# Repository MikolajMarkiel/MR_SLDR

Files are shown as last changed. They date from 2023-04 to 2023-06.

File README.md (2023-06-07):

# WARNING!

The project is in build stage. Missing documentation and functionalities will be added in time.

# Overview

The MR_SLDR is a project of remote controlled slider for camera. It will be controlled by Bluetooth Low Energy protocol. The main library source for this project is Zephyr OS.

# How to run

# Software description

## Web_bluetooth

## timer

Due to problems with flexibility occurence of threads in zephyr (minimal period step is 100us) I've decided to leave control of stepper motor up to hardware timer peripheral. Unfortunately right now esp32 timer drivers are dedicated only for counters that lose synchronization after overflow of counted ticks. Because of that I had to add extra modification to counter_esp32_tmr.c file (this file is a driver to handle every action of timer after setting devicetree &timerX status = "okay"). The modification allow us to decide that counter will autoreset after getting alarm or won't. It doesn't harm any project that use old driver, because for this to work user has to add extra `COUNTER_AUTORESET` config to Kconfig file. I've included new counter_esp32_tmr.c file in bin/ directory. The path for replacement is `../zephyrproject/zephyr/drivers/counter/counter_esp32_tmr.c`

## Distance_meter

# Hardware description

## Power section

The main supply for the board is +5V microUSB port. It supplies two DC-DC converters: step-up to +12V and step-down to +3,3V. The +12 DC voltage is needed for charging alternative power supply based on 3 li-ion cells driven by BMS3451 BMS. If there is no USB cable connected, then step-down converter is supplied by +12V instead. There is an external switch that enables step-down converter. If it is disabled, then every peripheral would be powered down except stepper motor driver which would go into sleep mode instead. Connecting USB cable with switch turned off allow charging batteries without turning on the device.
Voltage level of cell block is continually checked by ADC, and the feedback information is given to user via BLE.

## CPU & programming

An ESP32 module has been chosen as a CPU for the device. It has been because of his low cost and support for bluetooth communication and zephyr OS. There are two ways to communicate PC with CPU: via CP2102 USB to UART bridge module connected to micro USB and JTAG connector. Both allow to program flash memory. Additionally the bridge provides serial communication with PC and JTAG give possibility to debug software.

## Stepper motor driver

DRV8825 module has been used as an output driver for stepper motor. It provides easy interface because of it's STEP/DIR functionality. For more information please refer to datasheet of module.

## Distance meter

For checking actual position of camera even after power off the laser distance meter VL53LXX module is connected to CPU by I2C interface. Because it is needed to connect module directly at path of moving camera, then the module has been removed from the main hardware PCB and case. For more information please refer to datasheet of module.

## Camera control blocks

There are also two isolated switches for example for activating remote control of camera or other these types activities. They are designed with use of single channel transoptors PC817.

## EEPROM

The board provides also external EEPROM (M93C76C module) for saving user data of slider settings. It communicates with CPU via SPI interface.

## Mechanicals

The board has been designed for Z57J universal case (https://www.kradex.com.pl/product/enclosures_hermetically_sealed/z57j_ps?lang=en) but it is also possible to print something similar. By now there is no need to provide additional 3D models of case.

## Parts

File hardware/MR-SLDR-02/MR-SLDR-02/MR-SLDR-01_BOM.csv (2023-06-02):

Source: | /home/mikolaj/projects/MR-SLDR/hardware/MR-SLDR-01/MR-SLDR-01.kicad_sch
Date: | pią, 2 cze 2023, 03:15:36
Tool: | Eeschema 7.0.2-6a45011f42~172~ubuntu22.04.1
Generator: | /usr/share/kicad/plugins/bom_csv_grouped_by_value.py
Component Count: | 139
Collated Components:
Item | Qty | Reference(s) | Value | LibPart | Footprint | Datasheet | DNP | MANUFACTURER | MAXIMUM_PACKAGE_HEIGHT | PARTREV | STANDARD | Sim.Device | Sim.Pins | Sim.Type
1 | 7 | Batt.meas1, TP3, TP4, TP5, TP6, TP7, TP8 | TestPoint | Connector:TestPoint | TestPoint:TestPoint_THTPad_1.0x1.0mm_Drill0.5mm | ~
2 | 2 | C1, C19 | 680uF | Device:C_Polarized | Capacitor_THT:CP_Radial_D10.0mm_P5.00mm | ~
3 | 15 | C2, C3, C4, C5, C6, C8, C9, C10, C12, C13, C15, C21, C22, C29, C30 | 100nF | Device:C | Capacitor_SMD:C_0805_2012Metric_Pad1.18x1.45mm_HandSolder | ~
4 | 2 | C11, C14 | 470uF | Device:C_Polarized | Capacitor_THT:CP_Radial_D8.0mm_P3.80mm | ~
5 | 1 | C16 | none | Device:C | Capacitor_SMD:C_0805_2012Metric_Pad1.18x1.45mm_HandSolder | ~
6 | 3 | C17, C18, C23 | 470nF | Device:C | Capacitor_SMD:C_0805_2012Metric_Pad1.18x1.45mm_HandSolder | ~
7 | 1 | C20 | 4.7uF | Device:C | Capacitor_SMD:C_1206_3216Metric_Pad1.33x1.80mm_HandSolder | ~
8 | 1 | C24 | 100uF | Device:C_Polarized | Capacitor_THT:CP_Radial_D8.0mm_P3.80mm | ~
9 | 4 | C25, C26, C27, C28 | 10nF | Device:C | Capacitor_SMD:C_0805_2012Metric_Pad1.18x1.45mm_HandSolder | ~
10 | 3 | D1, D2, D3 | SS24 | SS24:SS24 | bin:DIOM5336X265N |  |  | ON Semiconductor | 2.65 mm | 1.1.2 | IPC 7351B
11 | 1 | D4 | SP0503BAHT | Power_Protection:SP0503BAHT | Package_TO_SOT_SMD:SOT-143 | http://www.littelfuse.com/~/media/files/littelfuse/technical%20resources/documents/data%20sheets/sp05xxba.pdf
12 | 1 | D5 | 10V | Device:D_Zener | Diode_SMD:D_MiniMELF | ~
13 | 1 | D6 | BAT54S | Diode:BAT54S | Package_TO_SOT_SMD:SOT-23 | https://www.diodes.com/assets/Datasheets/ds11005.pdf
14 | 1 | F1 | Fuse | Device:Fuse | Fuse:Fuse_1206_3216Metric_Pad1.42x1.75mm_HandSolder | ~
15 | 4 | H1, H2, H3, H4 | MountingHole | Mechanical:MountingHole | MountingHole:MountingHole_3.2mm_M3 | ~
16 | 4 | J1, J8, J9, J10 | Conn_01x02_Pin | Connector:Conn_01x02_Pin | Connector_Molex:Molex_SL_171971-0002_1x02_P2.54mm_Vertical | ~
17 | 1 | J2 | Conn_01x04_Pin | Connector:Conn_01x04_Pin | Connector_Molex:Molex_KK-254_AE-6410-04A_1x04_P2.54mm_Vertical | ~
18 | 1 | J3 | USB_B_Micro | Connector:USB_B_Micro | Connector_USB:USB_Micro-B_Amphenol_10118194_Horizontal | ~
19 | 1 | J4 | Conn_02x05_Odd_Even | Connector_Generic:Conn_02x05_Odd_Even | Connector_PinHeader_2.00mm:PinHeader_2x05_P2.00mm_Vertical | ~
20 | 1 | J5 | Conn_01x04_Socket | Connector:Conn_01x04_Socket | Connector_Molex:Molex_KK-254_AE-6410-04A_1x04_P2.54mm_Vertical | ~
21 | 1 | J6 | Conn_01x06_Pin | Connector:Conn_01x06_Pin | Connector_Molex:Molex_KK-254_AE-6410-06A_1x06_P2.54mm_Vertical | ~
22 | 1 | J7 | Conn_02x04_Odd_Even | Connector_Generic:Conn_02x04_Odd_Even | Connector_PinSocket_2.54mm:PinSocket_2x04_P2.54mm_Vertical | ~
23 | 4 | JP1, JP7, JP8, JP9 | SolderJumper_2_Bridged | Jumper:SolderJumper_2_Bridged | Jumper:SolderJumper-2_P1.3mm_Bridged_RoundedPad1.0x1.5mm | ~
24 | 5 | JP2, JP3, JP4, JP5, JP6 | SolderJumper_2_Open | Jumper:SolderJumper_2_Open | Jumper:SolderJumper-2_P1.3mm_Open_RoundedPad1.0x1.5mm | ~
25 | 1 | L1 | 33uH | Device:L | Inductor_SMD:L_12x12mm_H8mm | ~
26 | 1 | L2 | 22uH | Device:L | Inductor_SMD:L_TDK_VLF10040 | ~
27 | 6 | Q1, Q2, Q6, Q7, Q8, Q9 | BC817 | Transistor_BJT:BC817 | Package_TO_SOT_SMD:SOT-23 | https://www.onsemi.com/pub/Collateral/BC818-D.pdf
28 | 1 | Q3 | IRLML6402 | Transistor_FET:IRLML6402 | Package_TO_SOT_SMD:SOT-23 | https://www.infineon.com/dgdl/irlml6402pbf.pdf?fileId=5546d462533600a401535668d5c2263c
29 | 2 | Q4, Q5 | QM6006D | Transistor_FET:QM6006D | Package_TO_SOT_SMD:TO-252-2 | http://www.jaolen.com/images/pdf/QM6006D.pdf |  |  |  |  |  | NMOS | 1=D 2=G 3=S | VDMOS
30 | 14 | R1, R2, R3, R7, R14, R15, R16, R19, R26, R30, R31, R43, R44, R47 | 1k | Device:R | Resistor_SMD:R_0805_2012Metric_Pad1.20x1.40mm_HandSolder | ~
31 | 2 | R4, R8 | 5M | Device:R | Resistor_SMD:R_0805_2012Metric_Pad1.20x1.40mm_HandSolder | ~
32 | 3 | R5, R10, R20 | 3k | Device:R | Resistor_SMD:R_0805_2012Metric_Pad1.20x1.40mm_HandSolder | ~
33 | 1 | R6 | 220k | Device:R | Resistor_SMD:R_0805_2012Metric_Pad1.20x1.40mm_HandSolder | ~
34 | 3 | R9, R11, R35 | 1M | Device:R | Resistor_SMD:R_0805_2012Metric_Pad1.20x1.40mm_HandSolder | ~
35 | 7 | R12, R32, R33, R34, R38, R41, R42 | 10k | Device:R | Resistor_SMD:R_0805_2012Metric_Pad1.20x1.40mm_HandSolder | ~
36 | 1 | R13 | 2k | Device:R | Resistor_SMD:R_0805_2012Metric_Pad1.20x1.40mm_HandSolder | ~
37 | 4 | R17, R18, R22, R23 | 5m | Device:R | Resistor_SMD:R_2512_6332Metric_Pad1.40x3.35mm_HandSolder | ~
38 | 1 | R21 | 1.8k | Device:R | Resistor_SMD:R_0805_2012Metric_Pad1.20x1.40mm_HandSolder | ~
39 | 4 | R24, R39, R40, R48 | 100k | Device:R | Resistor_SMD:R_0805_2012Metric_Pad1.20x1.40mm_HandSolder | ~
40 | 1 | R25 | 11k | Device:R | Resistor_SMD:R_0805_2012Metric_Pad1.20x1.40mm_HandSolder | ~
41 | 1 | R27 | 24k | Device:R | Resistor_SMD:R_0805_2012Metric_Pad1.20x1.40mm_HandSolder | ~
42 | 1 | R28 | 47k | Device:R | Resistor_SMD:R_0805_2012Metric_Pad1.20x1.40mm_HandSolder | ~
43 | 1 | R29 | 4,7k | Device:R | Resistor_SMD:R_0805_2012Metric_Pad1.20x1.40mm_HandSolder | ~
44 | 2 | R36, R37 | 100m | Device:R | Resistor_SMD:R_1206_3216Metric_Pad1.30x1.75mm_HandSolder | ~
45 | 3 | R45, R46, R49 | none | Device:R | Resistor_SMD:R_0805_2012Metric_Pad1.20x1.40mm_HandSolder | ~
46 | 1 | RN1 | 1k | Device:R_Pack04 | Resistor_SMD:R_Array_Convex_4x1206 | ~
47 | 1 | RV1 | 100k | Device:R_Potentiometer | Potentiometer_THT:Potentiometer_Bourns_3296W_Vertical | ~
48 | 1 | TP1 | +3.3V | Connector:TestPoint | TestPoint:TestPoint_THTPad_1.0x1.0mm_Drill0.5mm | ~
49 | 1 | TP2 | +12V | Connector:TestPoint | TestPoint:TestPoint_THTPad_1.0x1.0mm_Drill0.5mm | ~
50 | 1 | U1 | BM3451 | BM3451:BM3451(20pin) | Package_SO:TSSOP-20_4.4x6.5mm_P0.65mm
51 | 1 | U2 | ~ | axelite:AX3007ESA | Package_SO:SOIC-8-1EP_3.9x4.9mm_P1.27mm_EP2.29x3mm
52 | 1 | U3 | ~ | axelite:AX5201 | Package_SO:SOIC-8-1EP_3.9x4.9mm_P1.27mm_EP2.29x3mm
53 | 1 | U4 | ESP32-WROOM-E | Espressif:ESP32-WROOM-E | Espressif:ESP32-WROOM-32E | https://www.espressif.com/sites/default/files/documentation/esp32-wroom-32e_esp32-wroom-32ue_datasheet_en.pdf
54 | 1 | U5 | CP2102N-Axx-xQFN28 | Interface_USB:CP2102N-Axx-xQFN28 | Package_DFN_QFN:QFN-28-1EP_5x5mm_P0.5mm_EP3.35x3.35mm | https://www.silabs.com/documents/public/data-sheets/cp2102n-datasheet.pdf
55 | 1 | U6 | DRV8825 | DRV8825:DRV8825 | Package_SO:HTSSOP-28-1EP_4.4x9.7mm_P0.65mm_EP3.4x9.5mm_ThermalVias
56 | 1 | U7 | 93CxxC | Memory_EEPROM:93CxxC | Package_SO:SO-8_3.9x4.9mm_P1.27mm | http://ww1.microchip.com/downloads/en/DeviceDoc/20001749K.pdf
57 | 2 | U8, U9 | PC817 | Isolator:PC817 | Package_DIP:DIP-4_W7.62mm | http://www.soselectronic.cz/a_info/resource/d/pc817.pdf

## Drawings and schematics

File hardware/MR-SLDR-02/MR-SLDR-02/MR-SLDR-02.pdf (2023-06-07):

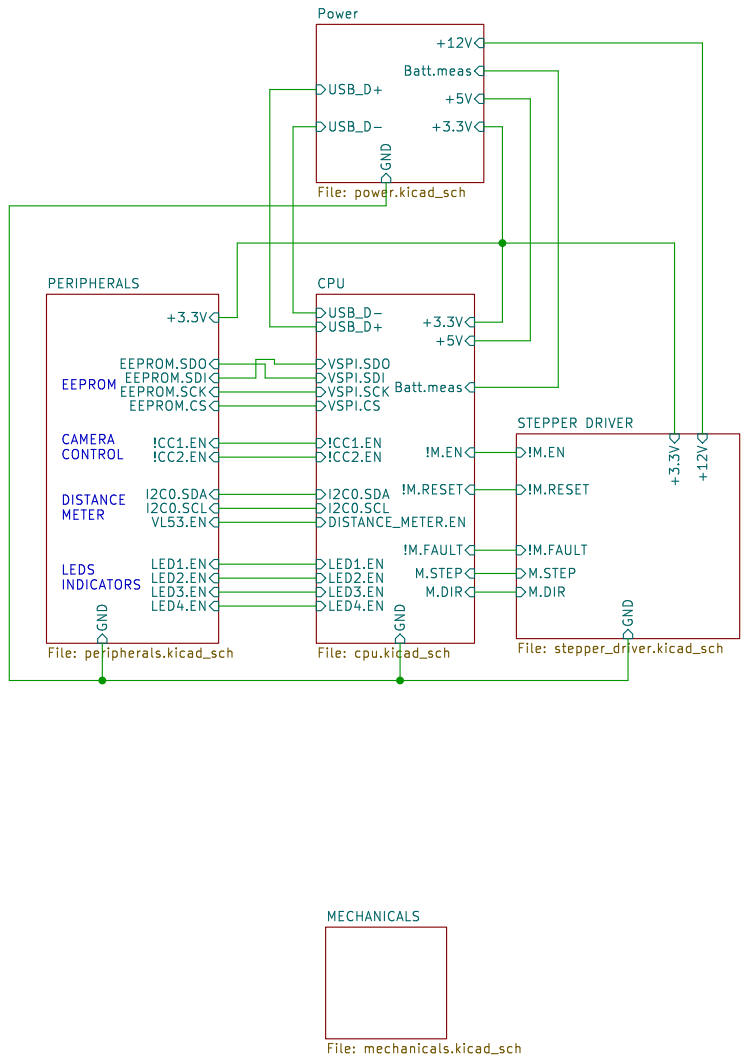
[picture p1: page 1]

Batt.meas Power File: power.kicad_sch GND

EEPROM.SDO
EEPROM.SDI EEPROM.CS
EEPROM.SCK

!M.FAULT VSPI.SDO
VSPI.SDI VSPI.SCK DISTANCE_METER.EN
VSPI.CS

CAMERA CONTROL DISTANCE METER

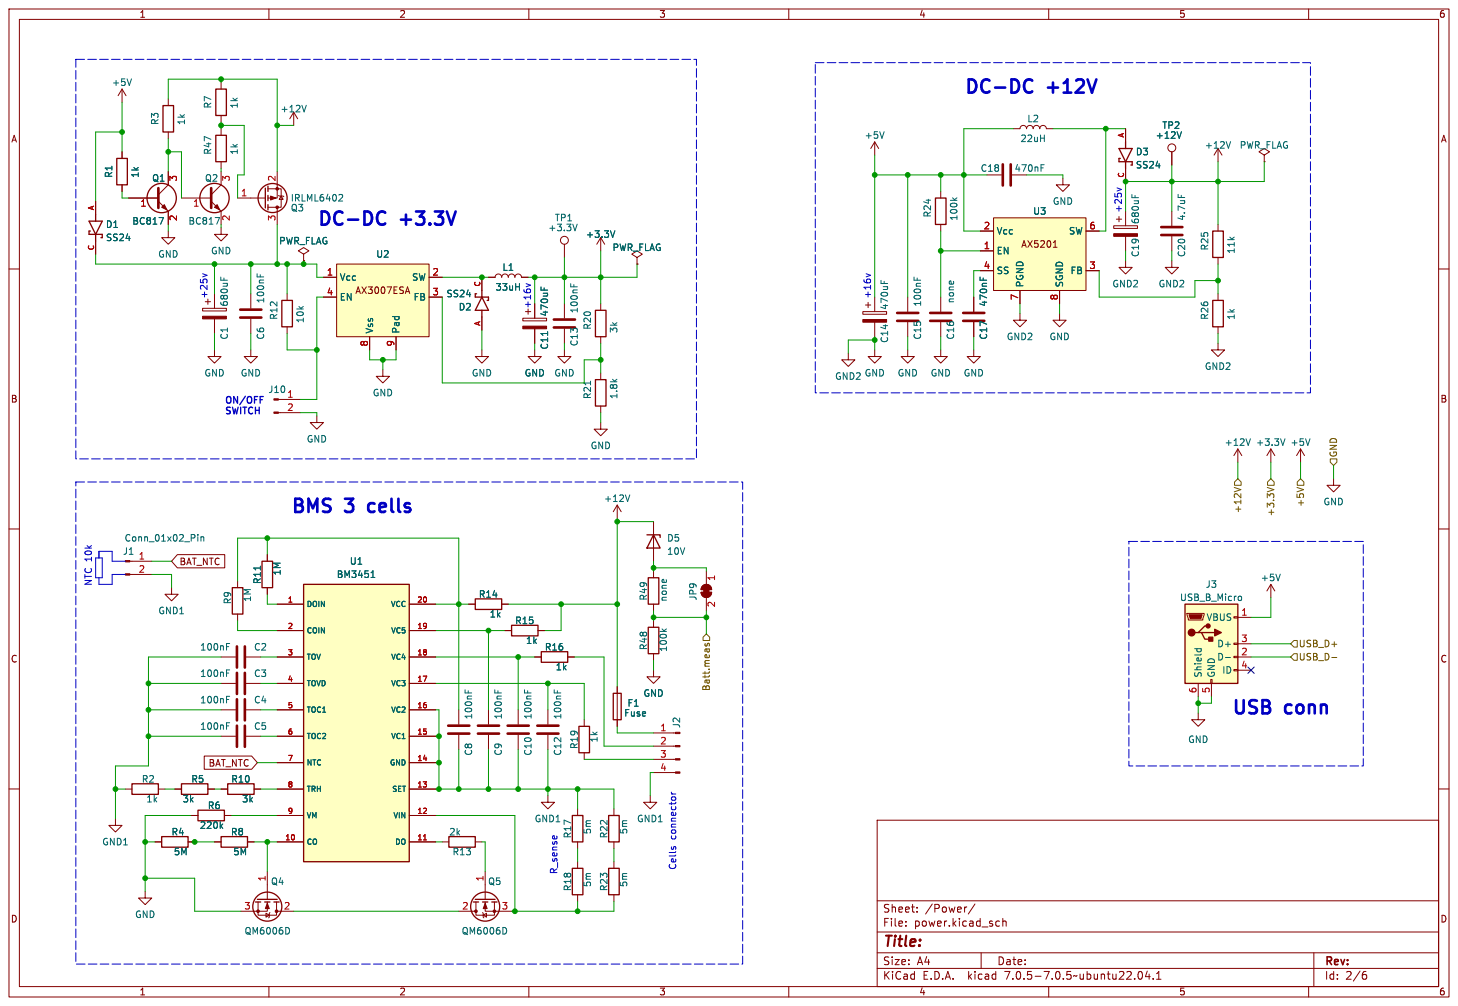
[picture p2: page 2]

A C U3 EN 1 Vcc 2 FB 3 SS 4 SW 6 PGND

Id: 2/6 Title: File: power.kicad_sch Sheet: /Power/

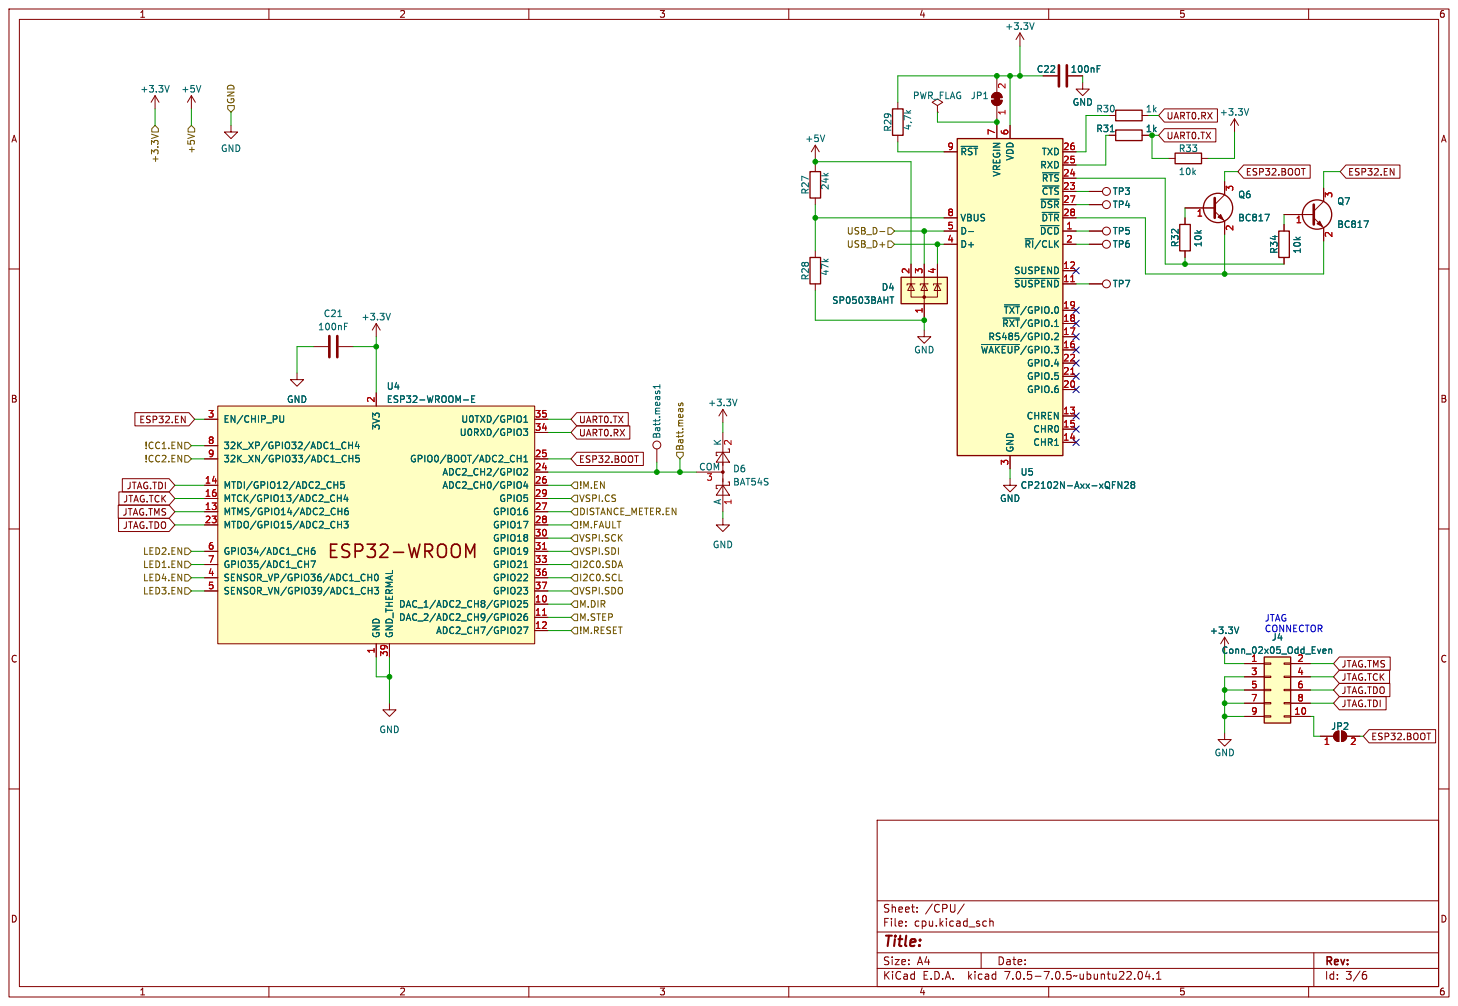
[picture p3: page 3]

4 U5 CP2102N-Axx-xQFN28 ~{DCD}1 ~{SUSPEND}11 SUSPEND 12 CHREN 13 CHR1 14 CHR0 15 ~{WAKEUP}/GPIO.316 RS485/GPIO.2 17 ~{RXT}/GPIO.118 ~{TXT}/GPIO.019 ~{RI}/CLK2 GPIO.6 20 GPIO.5 21 GPIO.4 22 ~{CTS} 23 ~{RTS} 24 RXD 25 TXD 26 ~{DSR} 27 ~{DTR} 28 GND

JTAG.TDI JTAG.TDO

DISTANCE_METER.EN
!M.FAULT VSPI.SDI VSPI.SCK

JTAG.TDI JTAG.TMS
JTAG.TCK
JTAG.TDO

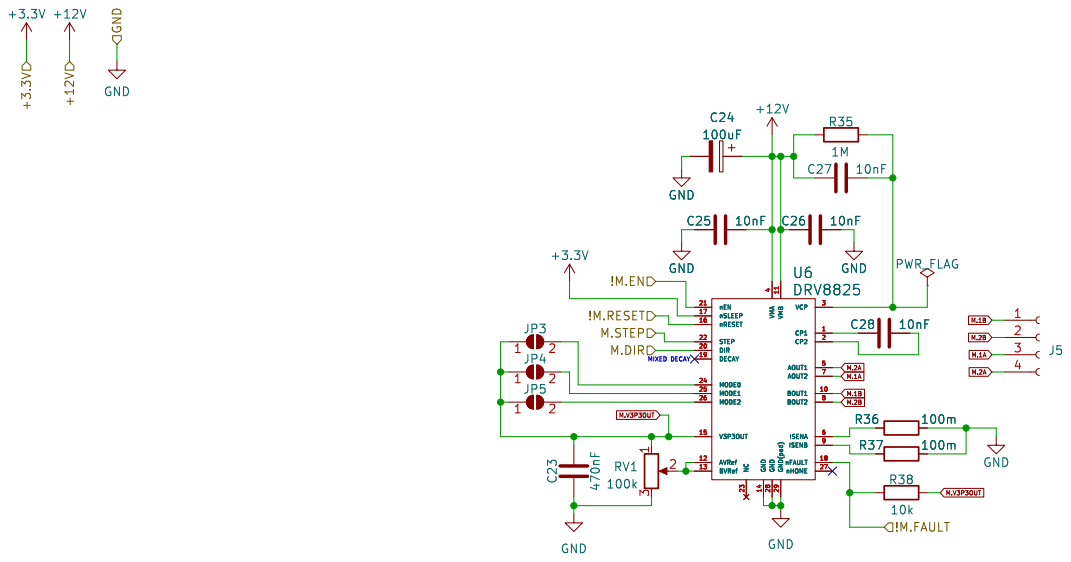
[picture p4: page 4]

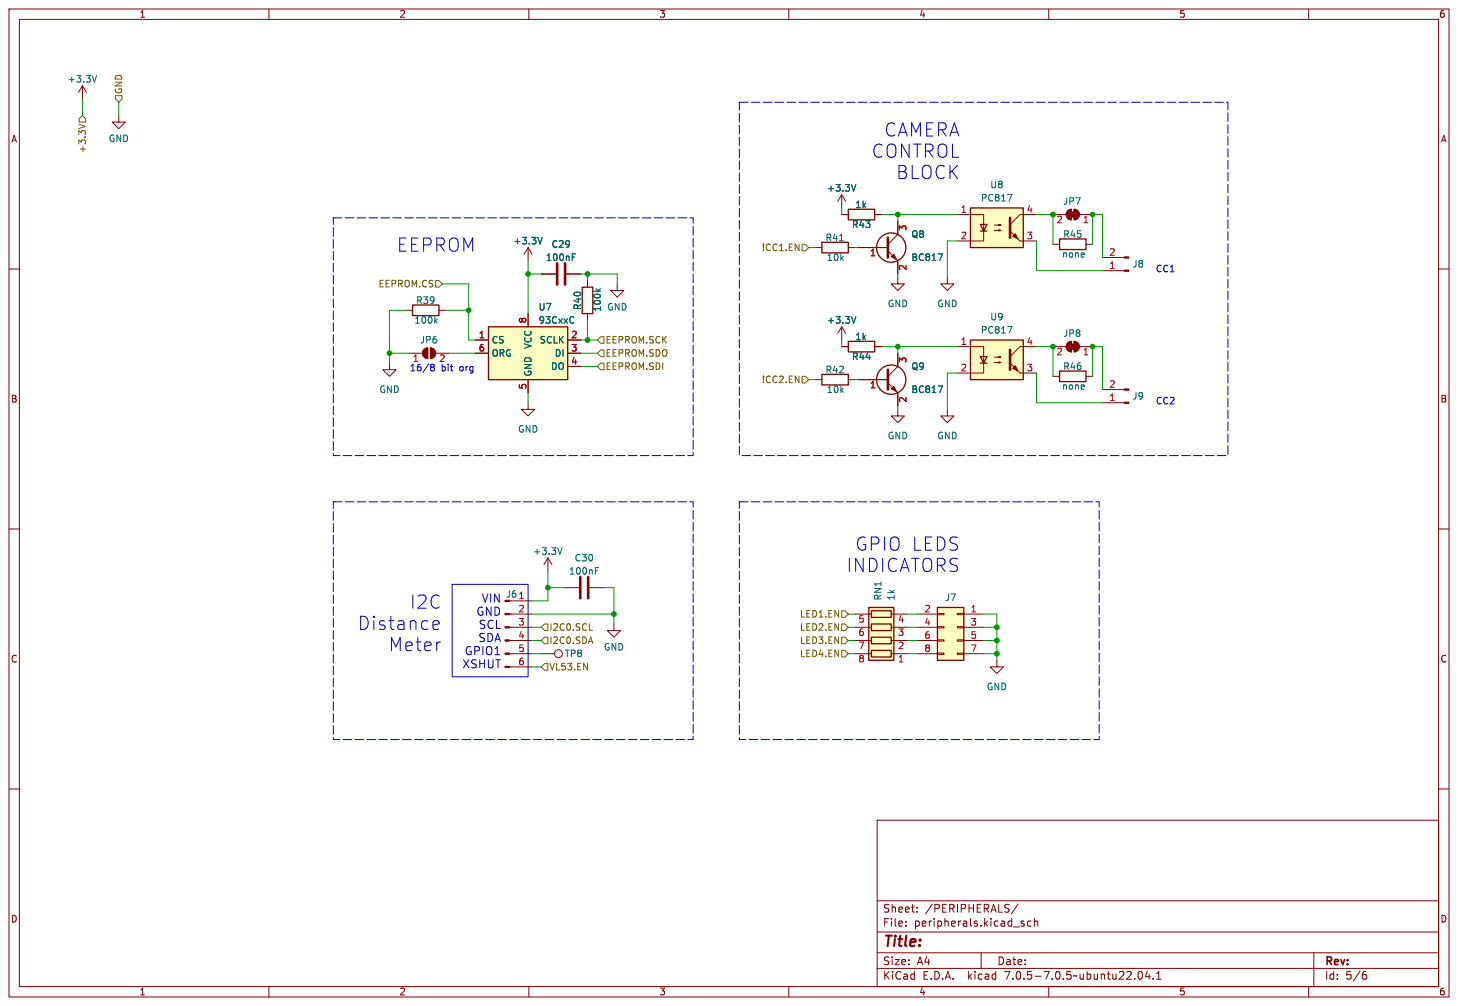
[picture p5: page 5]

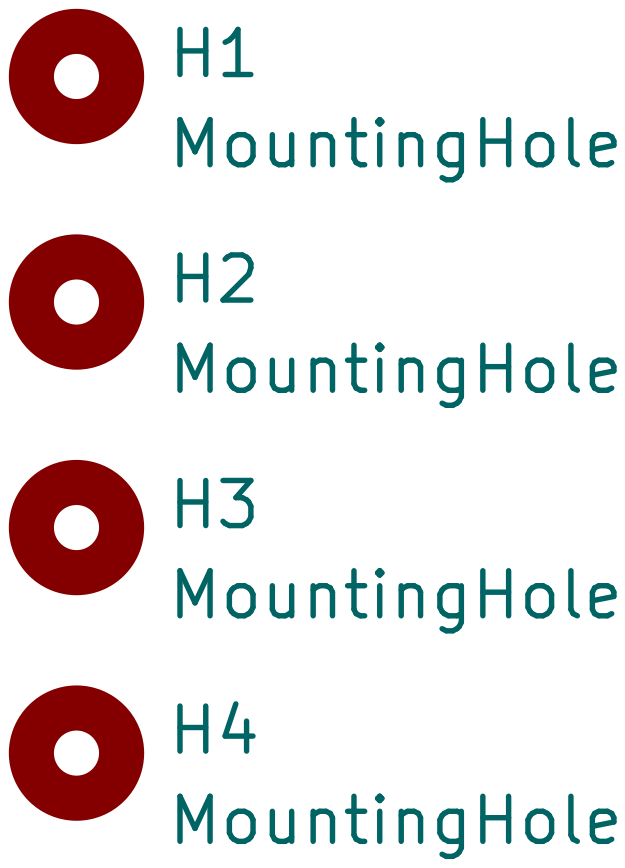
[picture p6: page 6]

H3 MountingHole H4 MountingHole H1 MountingHole H2 MountingHole

Id: 6/6 Title: File: mechanicals.kicad_sch Sheet: /MECHANICALS/

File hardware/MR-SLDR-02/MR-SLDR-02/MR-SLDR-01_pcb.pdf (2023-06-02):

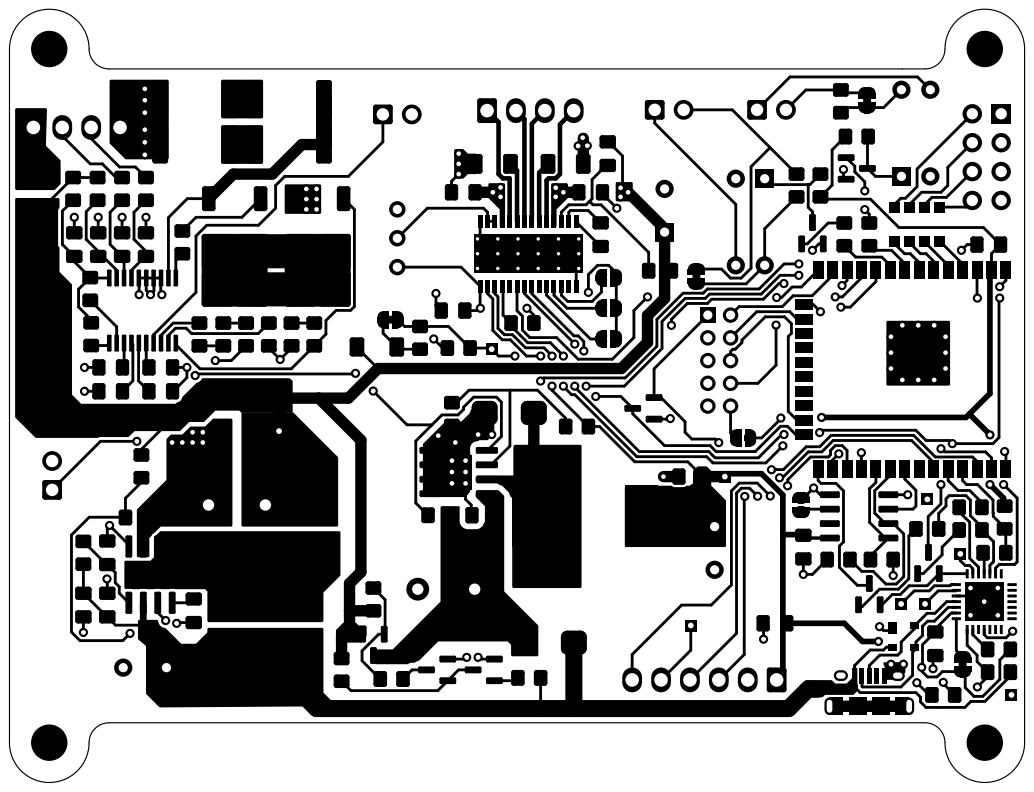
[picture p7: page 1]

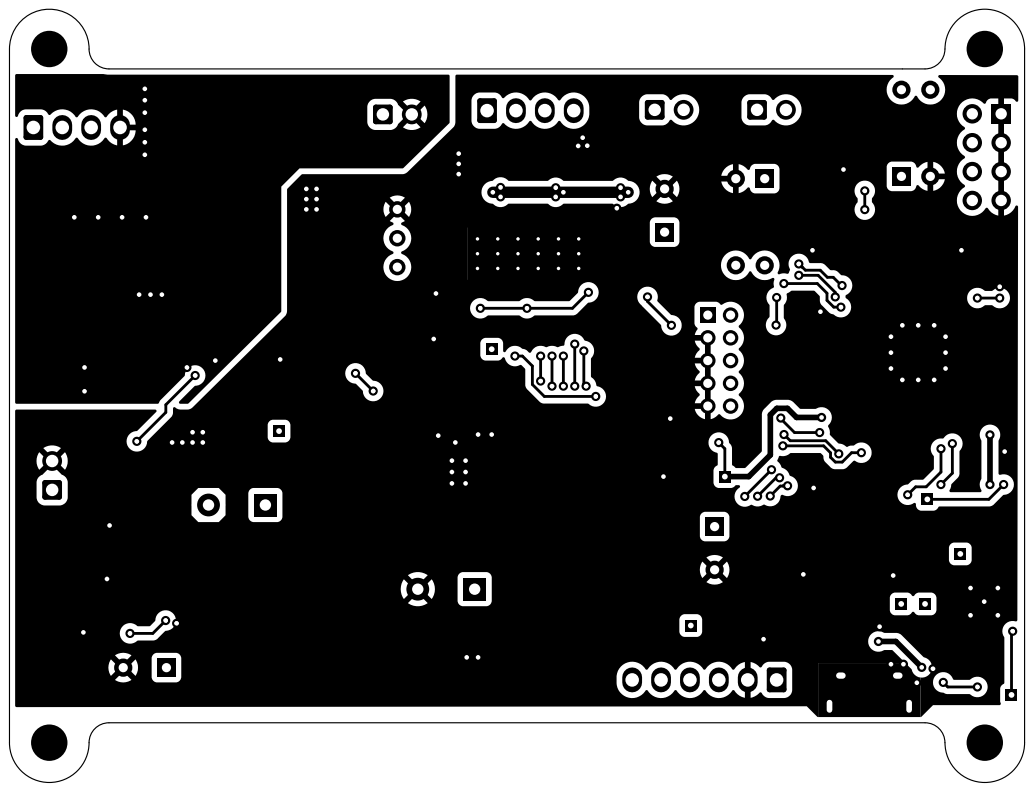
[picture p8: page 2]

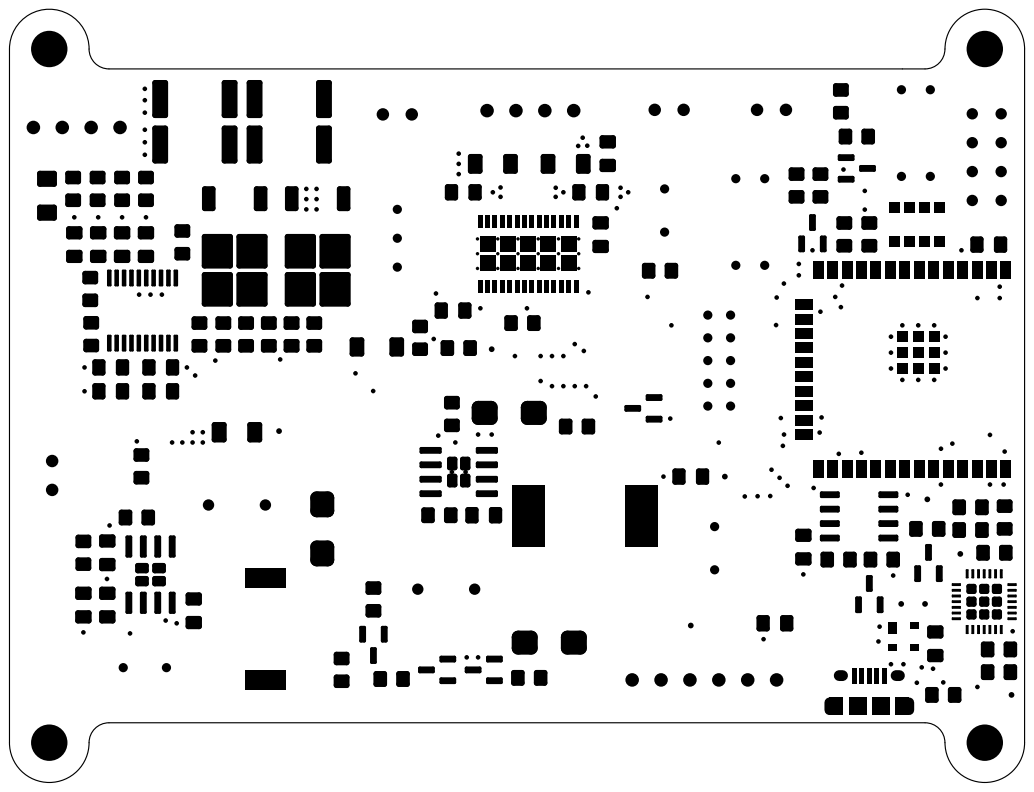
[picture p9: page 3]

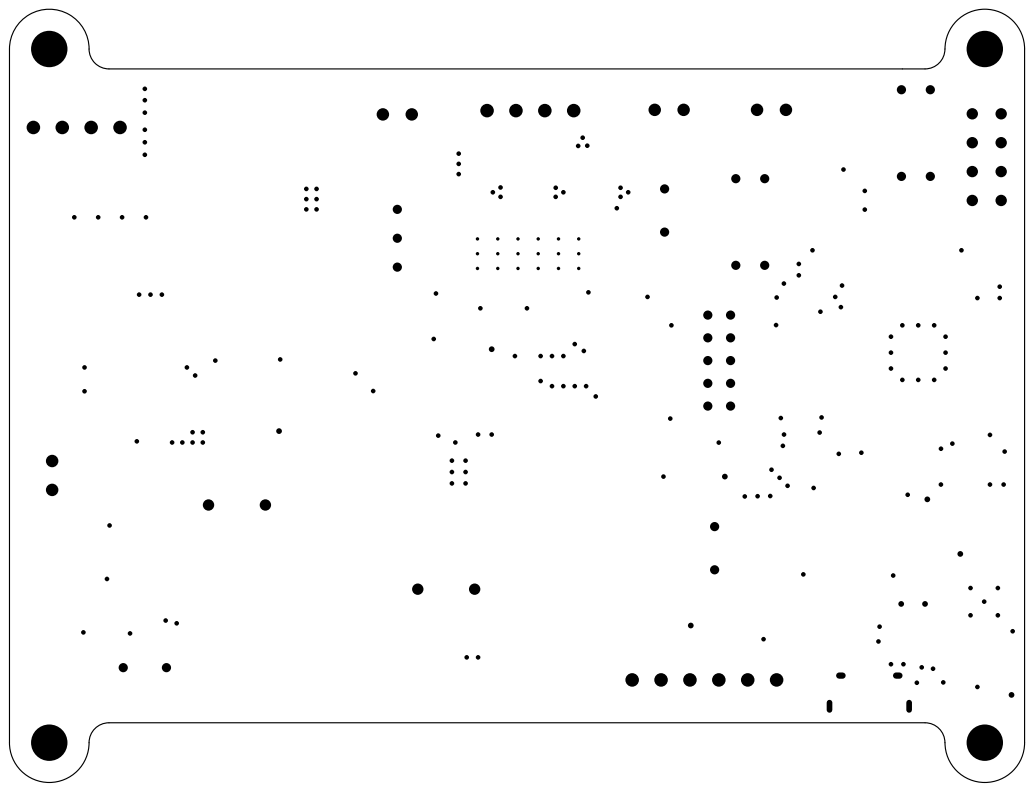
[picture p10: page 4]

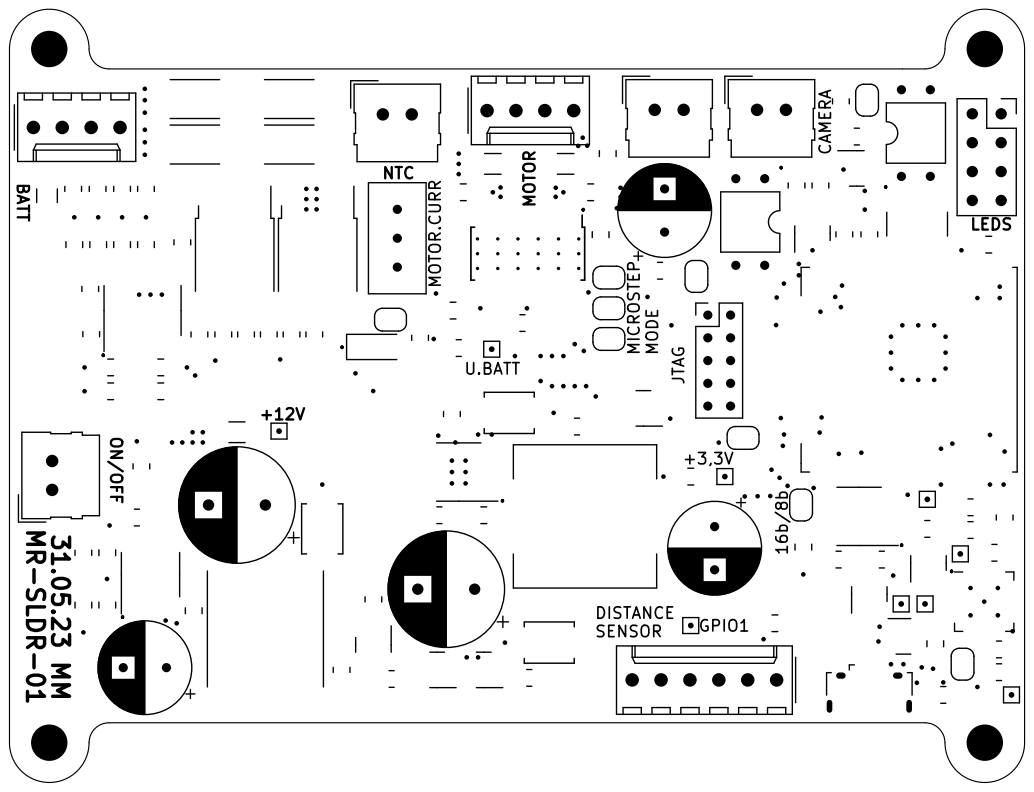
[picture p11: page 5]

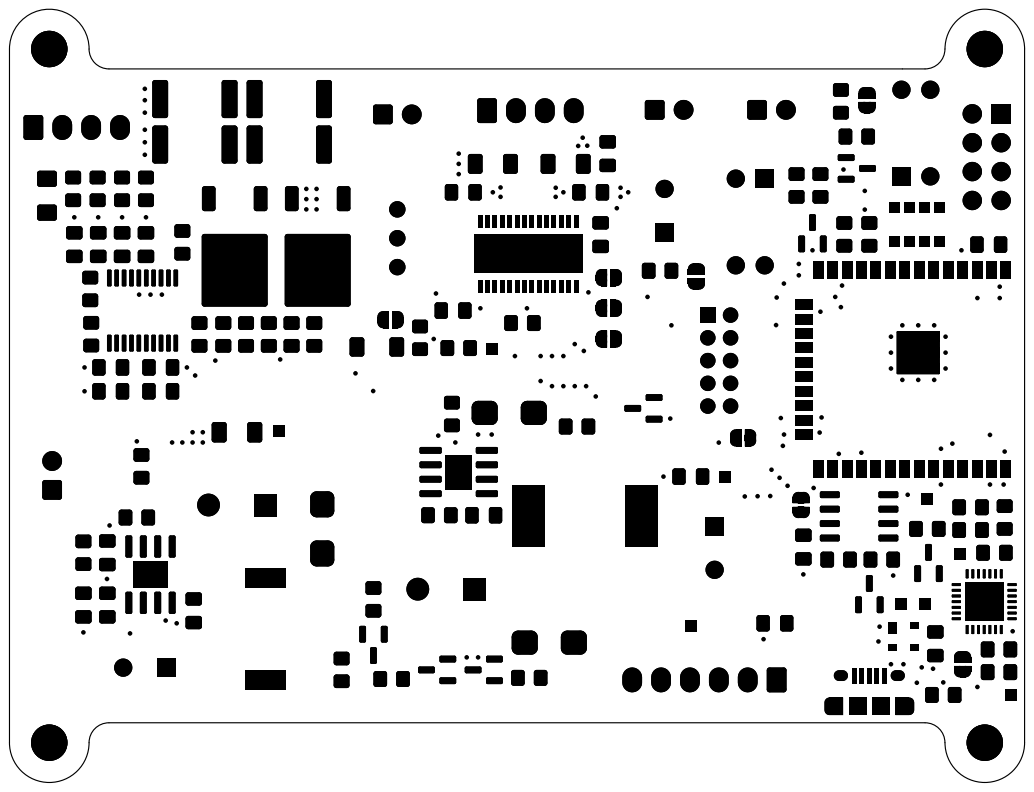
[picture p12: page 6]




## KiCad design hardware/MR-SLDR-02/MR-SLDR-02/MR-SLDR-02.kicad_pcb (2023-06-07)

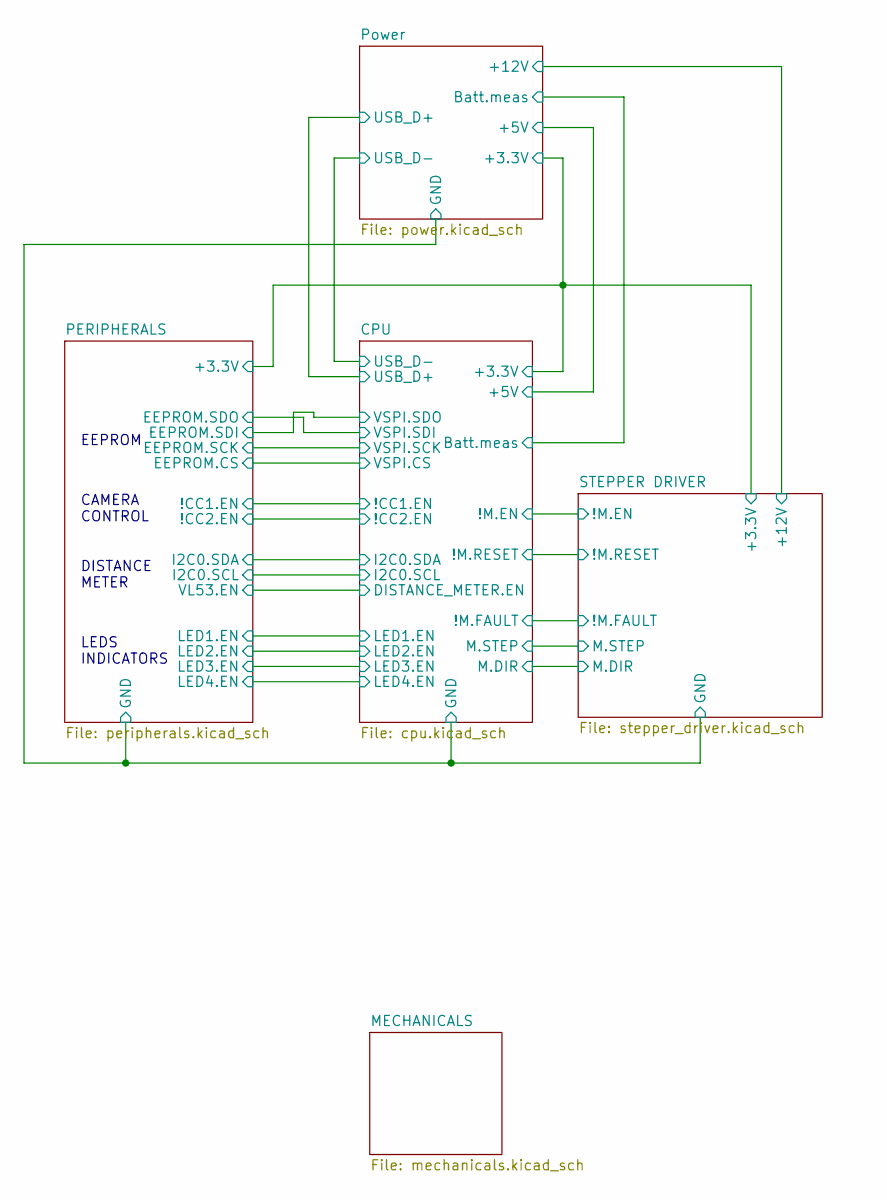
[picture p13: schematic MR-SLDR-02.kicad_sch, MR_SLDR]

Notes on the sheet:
LEDS INDICATORS
DISTANCE METER
CAMERA CONTROL
EEPROM

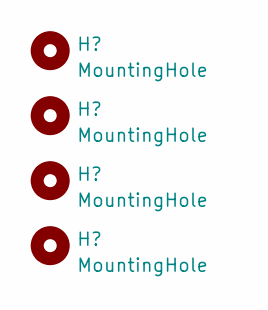
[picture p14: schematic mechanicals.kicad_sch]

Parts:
H1, H2, H3, H4: MountingHole; MountingHole_3.2mm_M3

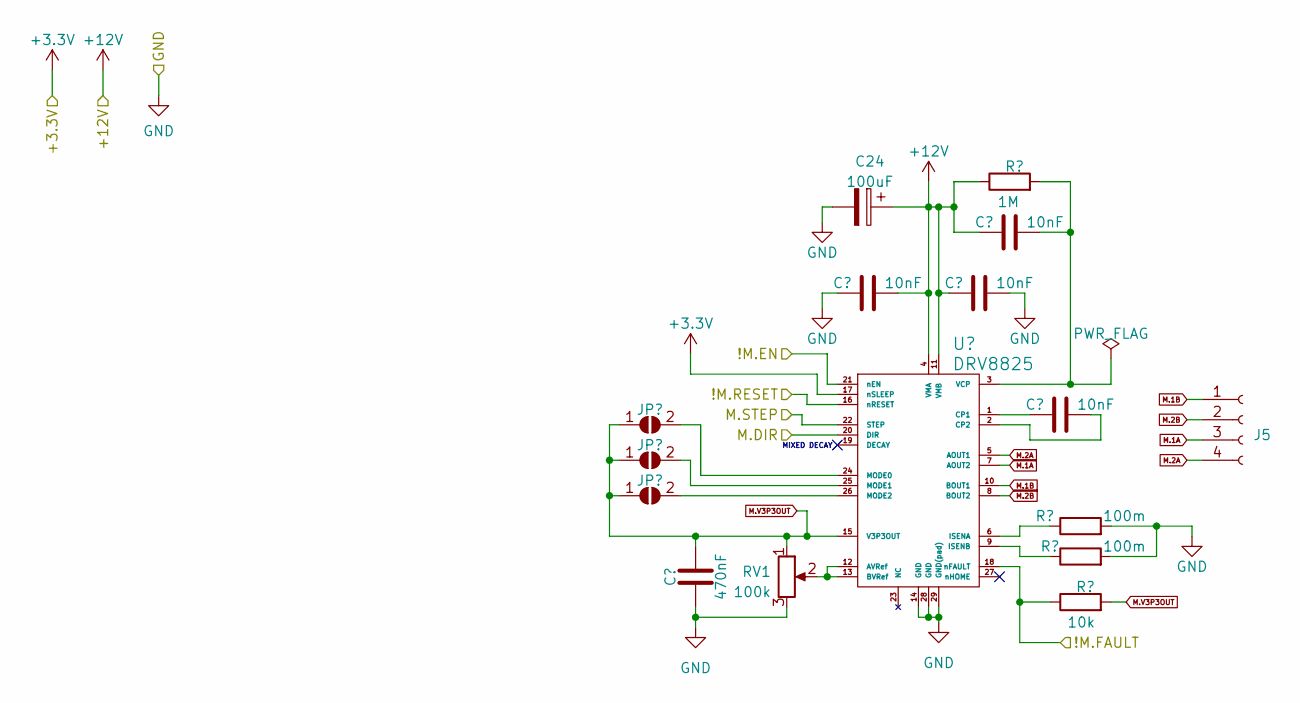
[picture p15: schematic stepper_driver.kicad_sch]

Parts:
C23: 470nF; C_0805_2012Metric_Pad1.18x1.45mm_HandSolder
C24: 100uF; CP_Radial_D8.0mm_P3.80mm
C25, C26, C27, C28: 10nF; C_0805_2012Metric_Pad1.18x1.45mm_HandSolder
J5: Conn_01x04_Socket; Molex_KK-254_AE-6410-04A_1x04_P2.54mm_Vertical
JP3, JP4, JP5: SolderJumper_2_Open; SolderJumper-2_P1.3mm_Open_RoundedPad1.0x1.5mm
R35: 1M; R_0805_2012Metric_Pad1.20x1.40mm_HandSolder
R36, R37: 100m; R_1206_3216Metric_Pad1.30x1.75mm_HandSolder
R38: 10k; R_0805_2012Metric_Pad1.20x1.40mm_HandSolder
RV1: 100k; Potentiometer_Bourns_3296W_Vertical
U6: DRV8825; HTSSOP-28-1EP_4.4x9.7mm_P0.65mm_EP3.4x9.5mm_ThermalVias

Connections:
+3.3V: U6.17 (nSLEEP); also elsewhere on the board
+12V: C24.1, C25.2, C26.1, C27.1, R35.1, U6.4 (VMA), U6.11 (VMB); also elsewhere on the board
/CPU/!M.EN: U6.21 (nEN); also elsewhere on the board
/CPU/!M.FAULT: R38.1, U6.18 (nFAULT); also elsewhere on the board
/CPU/!M.RESET: U6.16 (nRESET); also elsewhere on the board
/CPU/M.DIR: U6.20 (DIR); also elsewhere on the board
/CPU/M.STEP: U6.22 (STEP); also elsewhere on the board
GND: C23.1, C24.2, C25.1, C26.2, R36.2, R37.2, RV1.3, U6.14 (GND), U6.28 (GND), U6.29 (GND(pad)); also elsewhere on the board
M.1A: J5.3, U6.7 (AOUT2)
M.1B: J5.1, U6.10 (BOUT1)
M.2A: J5.4, U6.5 (AOUT1)
M.2B: J5.2, U6.8 (BOUT2)
M.V3P3OUT: C23.2, JP3.1 (A), JP4.1 (A), JP5.1 (A), R38.2, RV1.1, U6.15 (V3P3OUT)
unnamed: JP3.2 (B), U6.24 (MODE0)
unnamed: JP4.2 (B), U6.25 (MODE1)
unnamed: JP5.2 (B), U6.26 (MODE2)
unnamed: RV1.2, U6.12 (AVRef), U6.13 (BVRef)
unnamed: C28.1, U6.1 (CP1)
unnamed: C28.2, U6.2 (CP2)
unnamed: R36.1, U6.6 (ISENA)
unnamed: R37.1, U6.9 (ISENB)
unnamed: C27.2, R35.2, U6.3 (VCP)

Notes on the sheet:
MIXED DECAY

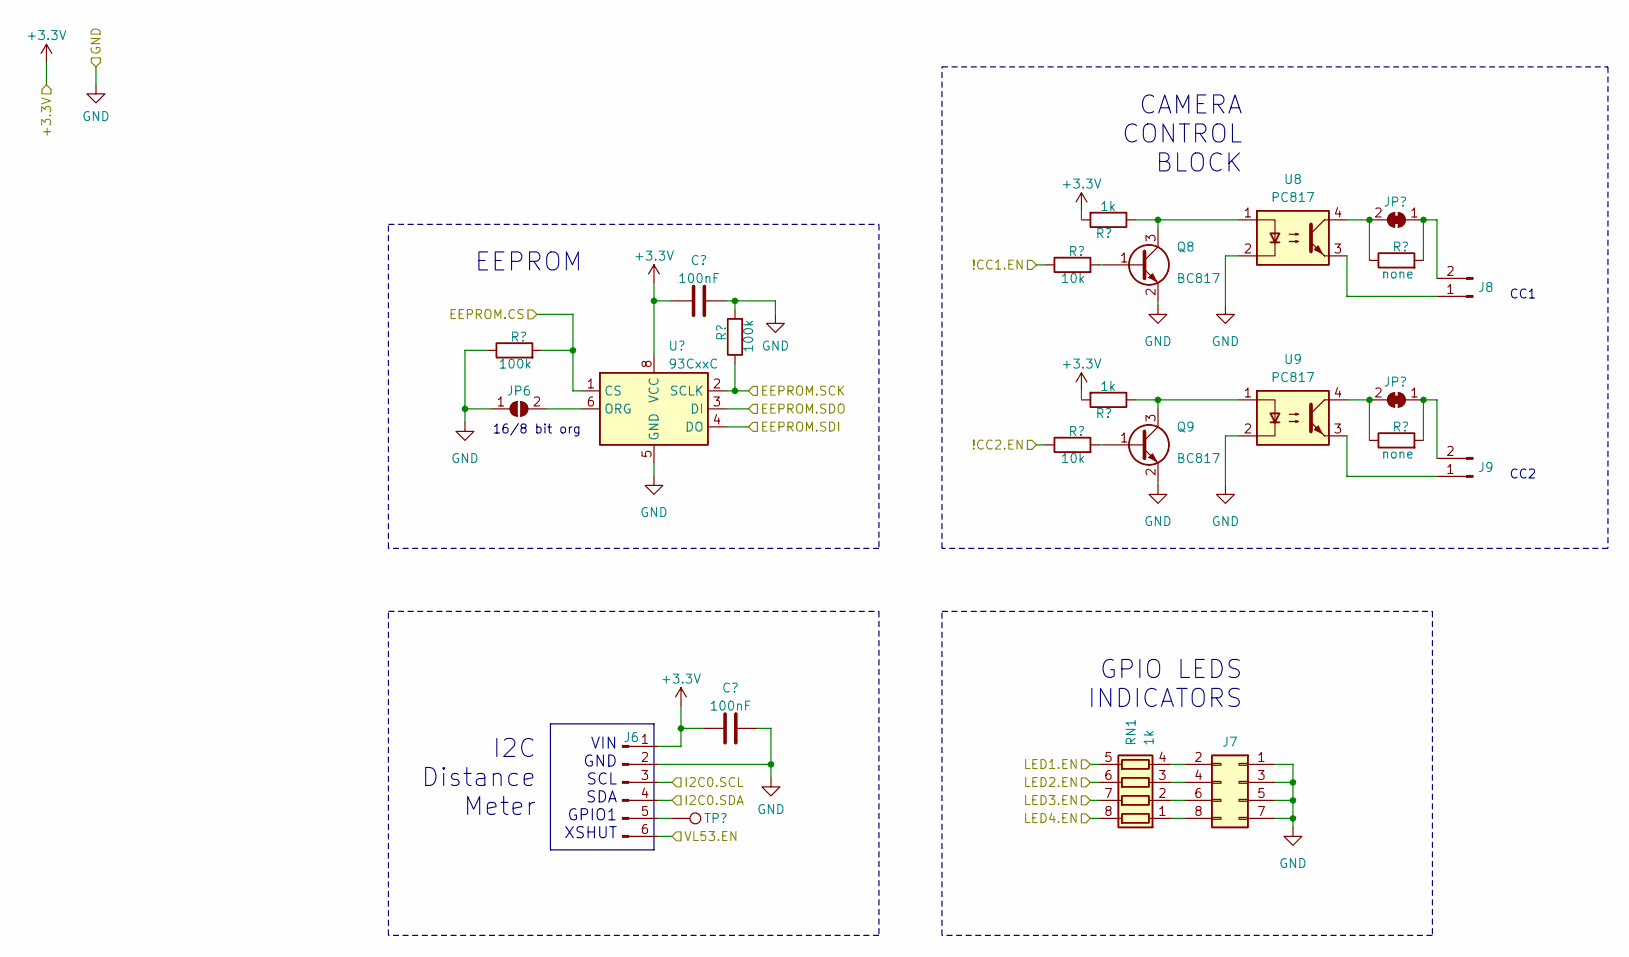
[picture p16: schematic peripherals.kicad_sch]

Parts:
C29, C30: 100nF; C_0805_2012Metric_Pad1.18x1.45mm_HandSolder
J6: Conn_01x06_Pin; Molex_KK-254_AE-6410-06A_1x06_P2.54mm_Vertical
J7: Conn_02x04_Odd_Even; PinSocket_2x04_P2.54mm_Vertical
J8, J9: Conn_01x02_Pin; Molex_SL_171971-0002_1x02_P2.54mm_Vertical
JP6: SolderJumper_2_Open; SolderJumper-2_P1.3mm_Open_RoundedPad1.0x1.5mm
JP7, JP8: SolderJumper_2_Bridged; SolderJumper-2_P1.3mm_Bridged_RoundedPad1.0x1.5mm
Q8, Q9: BC817; SOT-23
R39, R40: 100k; R_0805_2012Metric_Pad1.20x1.40mm_HandSolder
R41, R42: 10k; R_0805_2012Metric_Pad1.20x1.40mm_HandSolder
R43, R44: 1k; R_0805_2012Metric_Pad1.20x1.40mm_HandSolder
R45, R46: none; R_0805_2012Metric_Pad1.20x1.40mm_HandSolder
RN1: 1k; R_Array_Convex_4x0612
TP8: TestPoint; TestPoint_THTPad_1.0x1.0mm_Drill0.5mm
U7: 93CxxC; SO-8_3.9x4.9mm_P1.27mm
U8, U9: PC817; DIP-4_W7.62mm

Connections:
+3.3V: C29.2, C30.2, J6.1, R43.2, R44.2, U7.8 (VCC); also elsewhere on the board
/CPU/!CC1.EN: R41.1; also elsewhere on the board
/CPU/!CC2.EN: R42.1; also elsewhere on the board
/CPU/DISTANCE_METER.EN: J6.6; also elsewhere on the board
/CPU/I2C0.SCL: J6.3; also elsewhere on the board
/CPU/I2C0.SDA: J6.4; also elsewhere on the board
/CPU/LED1.EN: RN1.5 (R4.2); also elsewhere on the board
/CPU/LED2.EN: RN1.6 (R3.2); also elsewhere on the board
/CPU/LED3.EN: RN1.7 (R2.2); also elsewhere on the board
/CPU/LED4.EN: RN1.8 (R1.2); also elsewhere on the board
/CPU/VSPI.CS: R39.2, U7.1 (CS); also elsewhere on the board
/CPU/VSPI.SCK: R40.1, U7.2 (SCLK); also elsewhere on the board
/CPU/VSPI.SDI: U7.3 (DI); also elsewhere on the board
/CPU/VSPI.SDO: U7.4 (DO); also elsewhere on the board
GND: C29.1, C30.1, J6.2, J7.1, J7.3, J7.5, J7.7, JP6.1 (A), Q8.2 (E), Q9.2 (E), R39.1, R40.2, U7.5 (GND), U8.2, U9.2; also elsewhere on the board
unnamed: J6.5, TP8.1
unnamed: J7.2, RN1.4 (R4.1)
unnamed: J7.4, RN1.3 (R3.1)
unnamed: J7.6, RN1.2 (R2.1)
unnamed: J7.8, RN1.1 (R1.1)
unnamed: J8.1, U8.3
unnamed: J9.1, U9.3
unnamed: J9.2, JP8.1 (A), R46.2
unnamed: JP6.2 (B), U7.6 (ORG)
unnamed: JP8.2 (B), R46.1, U9.4
unnamed: Q8.1 (B), R41.2
unnamed: Q8.3 (C), R43.1, U8.1
unnamed: Q9.1 (B), R42.2
unnamed: Q9.3 (C), R44.1, U9.1

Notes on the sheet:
CC1
GPIO LEDS INDICATORS
CC2
16/8 bit org
VIN GND SCL SDA GPIO1 XSHUT
I2C Distance Meter
CAMERA CONTROL BLOCK
EEPROM

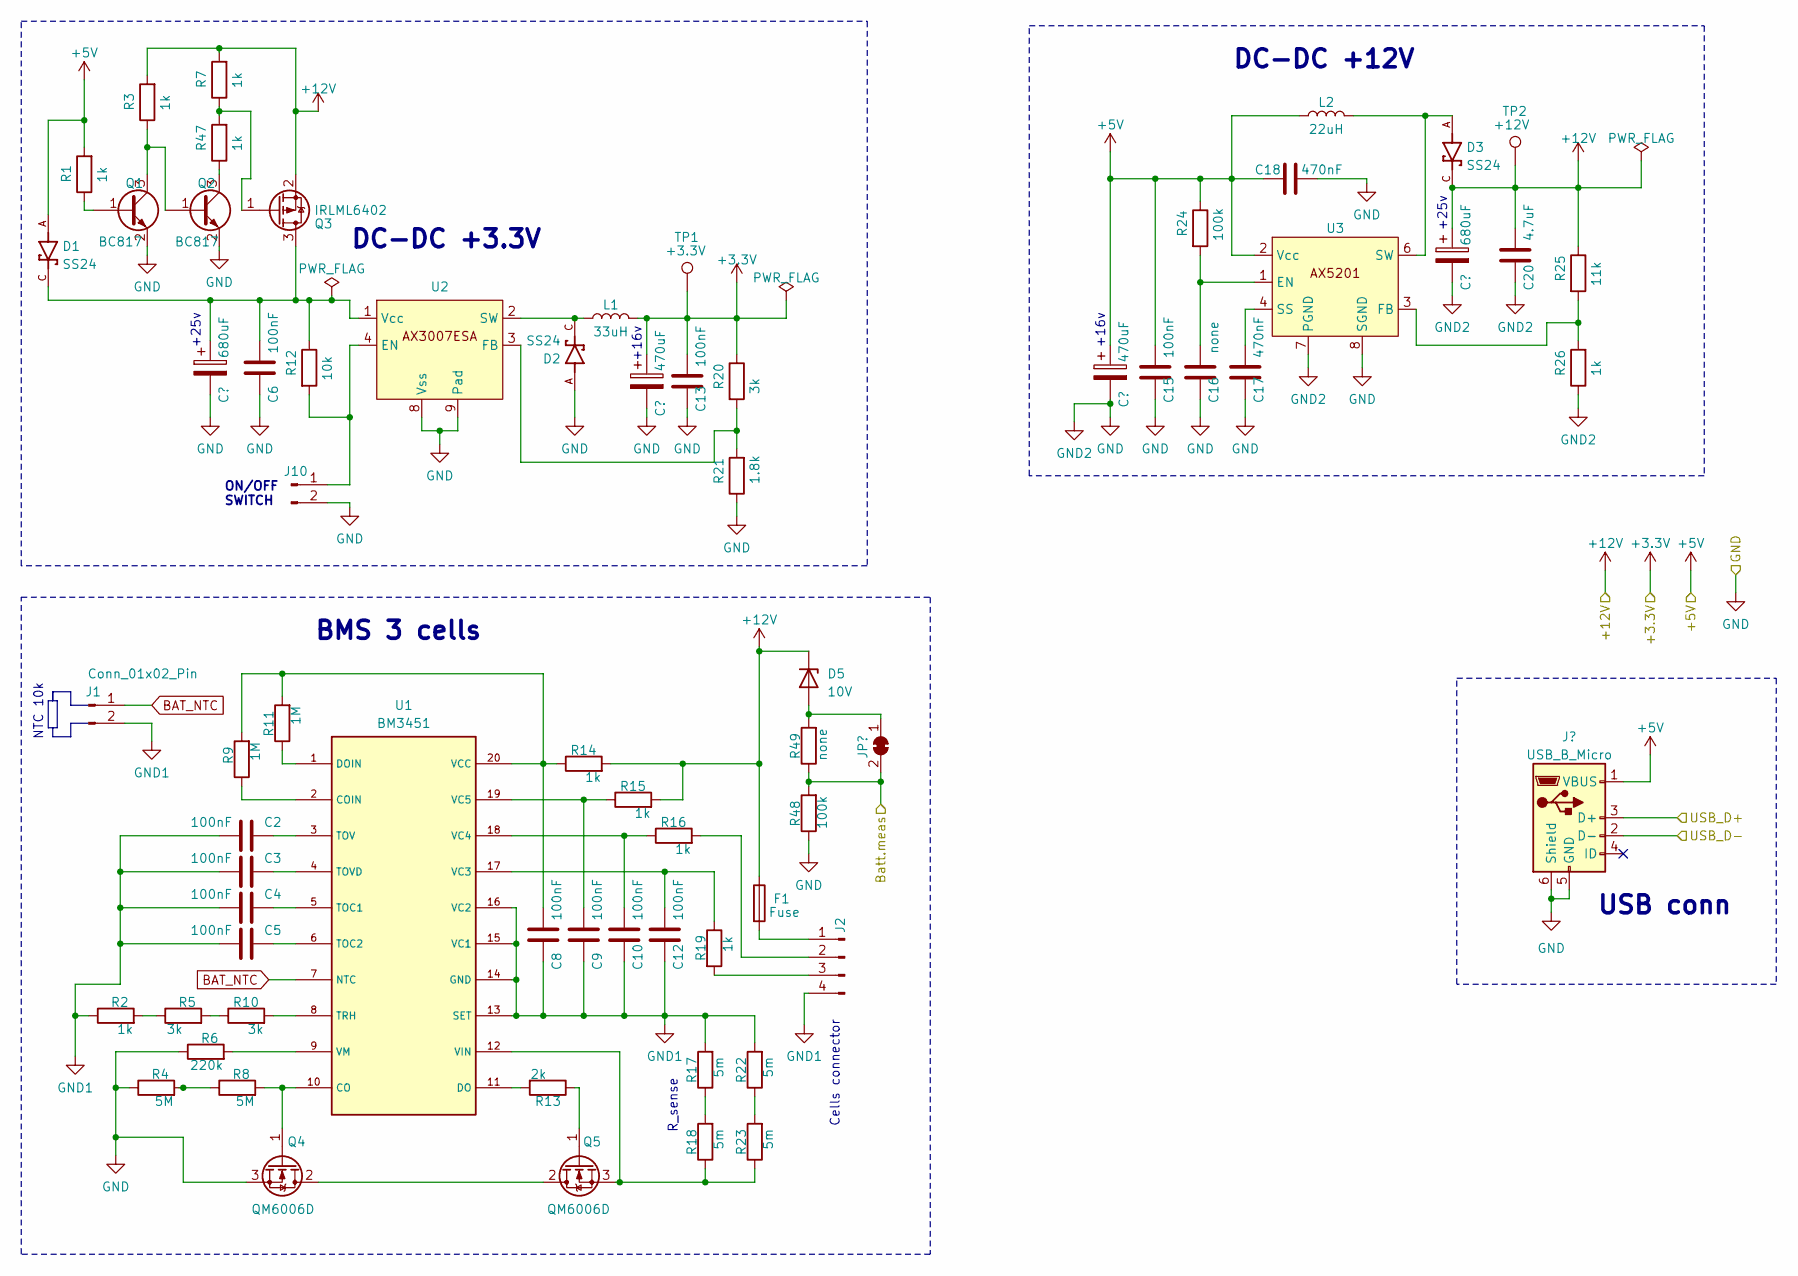
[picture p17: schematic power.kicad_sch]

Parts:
C1, C19: 680uF; CP_Radial_D10.0mm_P5.00mm
C2, C3, C4, C5, C6, C8, C9, C10, C12, C13, C15: 100nF; C_0805_2012Metric_Pad1.18x1.45mm_HandSolder
C11, C14: 470uF; CP_Radial_D8.0mm_P3.80mm
C16: none; C_0805_2012Metric_Pad1.18x1.45mm_HandSolder
C17, C18: 470nF; C_0805_2012Metric_Pad1.18x1.45mm_HandSolder
C20: 4.7uF; C_1206_3216Metric_Pad1.33x1.80mm_HandSolder
D1, D2, D3: SS24; DIOM5336X265N; PARTREV 1.1.2
D5: 10V; D_MiniMELF
F1: Fuse; Fuse_1206_3216Metric_Pad1.42x1.75mm_HandSolder
J1, J10: Conn_01x02_Pin; Molex_SL_171971-0002_1x02_P2.54mm_Vertical
J2: Conn_01x04_Pin; Molex_KK-254_AE-6410-04A_1x04_P2.54mm_Vertical
J3: USB_B_Micro; USB_Micro-B_Amphenol_10118194_Horizontal
JP7: SolderJumper_2_Bridged; SolderJumper-2_P1.3mm_Bridged_RoundedPad1.0x1.5mm
L1: 33uH; L_12x12mm_H8mm
L2: 22uH; L_TDK_VLF10040
Q1, Q2: BC817; SOT-23
Q3: IRLML6402; SOT-23
Q4, Q5: QM6006D; TO-252-2
R1, R2, R3, R7, R14, R15, R16, R19, R26, R47: 1k; R_0805_2012Metric_Pad1.20x1.40mm_HandSolder
R4, R8: 5M; R_0805_2012Metric_Pad1.20x1.40mm_HandSolder
R5, R10, R20: 3k; R_0805_2012Metric_Pad1.20x1.40mm_HandSolder
R6: 220k; R_0805_2012Metric_Pad1.20x1.40mm_HandSolder
R9, R11: 1M; R_0805_2012Metric_Pad1.20x1.40mm_HandSolder
R12: 10k; R_0805_2012Metric_Pad1.20x1.40mm_HandSolder
R13: 2k; R_0805_2012Metric_Pad1.20x1.40mm_HandSolder
R17, R18, R22, R23: 5m; R_2512_6332Metric_Pad1.40x3.35mm_HandSolder
R21: 1.8k; R_0805_2012Metric_Pad1.20x1.40mm_HandSolder
R24, R48: 100k; R_0805_2012Metric_Pad1.20x1.40mm_HandSolder
R25: 11k; R_0805_2012Metric_Pad1.20x1.40mm_HandSolder
R49: none; R_0805_2012Metric_Pad1.20x1.40mm_HandSolder
TP1: +3.3V; TestPoint_THTPad_1.0x1.0mm_Drill0.5mm
TP2: +12V; TestPoint_THTPad_1.0x1.0mm_Drill0.5mm
U1: BM3451; TSSOP-20_4.4x6.5mm_P0.65mm
U2, U3: SOIC-8-1EP_3.9x4.9mm_P1.27mm_EP2.29x3mm

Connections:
+3.3V: C11.1, C13.1, L1.2, R20.1, TP1.1; also elsewhere on the board
+5V: C14.1, C15.1, C18.1, D1.A, J3.1 (VBUS), L2.1, R1.2, R24.1, U3.2 (Vcc); also elsewhere on the board
+12V: C19.1, C20.1, D3.C, D5.1 (K), F1.1, Q3.2 (S), R3.2, R7.2, R14.2, R15.2, R25.1, TP2.1; also elsewhere on the board
/CPU/USB_D+: J3.3 (D+); also elsewhere on the board
/CPU/USB_D-: J3.2 (D-); also elsewhere on the board
BAT_NTC: J1.1, U1.7 (NTC)
GND: C1.2, C6.2, C11.2, C13.2, C14.2, C15.2, C16.2, C17.2, C18.2, C19.2, C20.2, D2.A, J3.5 (GND), J3.6 (Shield), J10.2, Q1.2 (E), Q2.2 (E), Q4.3 (S), R4.1, R6.1, R21.1, R26.1, R48.1, U2.5 (Vss), U2.6 (Vss), U2.7 (Vss), U2.8 (Vss), U2.9 (Pad), U3.7 (PGND), U3.8 (SGND); also elsewhere on the board
GND1: C2.1, C3.1, C4.1, C5.1, C8.2, C9.2, C10.2, C12.2, J1.2, J2.4, R2.1, R17.2, R22.2, U1.13 (SET), U1.14 (GND), U1.15 (VC1), U1.16 (VC2)
unnamed: D3.A, L2.2, U3.5 (SW), U3.6 (SW), U3.9 (Pad)
unnamed: F1.2, J2.1
unnamed: J2.2, R16.2
unnamed: J2.3, R19.2
unnamed: J10.1, R12.2, U2.4 (EN)
unnamed: Q1.1 (B), R1.1
unnamed: Q1.3 (C), Q2.1 (B), R3.1
unnamed: Q2.3 (C), R47.1
unnamed: C1.1, C6.1, D1.C, Q3.3 (D), R12.1, U2.1 (Vcc)
unnamed: Q3.1 (G), R7.1, R47.2
unnamed: Q4.2 (D), Q5.2 (D)
unnamed: Q4.1 (G), R8.2, U1.10 (CO)
unnamed: Q5.1 (G), R13.1
unnamed: Q5.3 (S), R18.1, R23.1, U1.12 (VIN)
unnamed: R2.2, R5.1
unnamed: R4.2, R8.1
unnamed: R5.2, R10.1
unnamed: R17.1, R18.2
unnamed: R22.1, R23.2
unnamed: R9.1, U1.2 (COIN)
unnamed: R13.2, U1.11 (DO)
unnamed: R11.1, U1.1 (DOIN)
unnamed: C4.2, U1.5 (TOC1)
unnamed: C5.2, U1.6 (TOC2)
unnamed: C2.2, U1.3 (TOV)
unnamed: C3.2, U1.4 (TOVD)
unnamed: R10.2, U1.8 (TRH)
unnamed: C12.1, R19.1, U1.17 (VC3)
unnamed: C10.1, R16.1, U1.18 (VC4)
unnamed: C9.1, R15.1, U1.19 (VC5)
unnamed: C8.1, R9.2, R11.2, R14.1, U1.20 (VCC)
unnamed: R6.2, U1.9 (VM)
unnamed: R20.2, R21.2, U2.3 (FB)
unnamed: D2.C, L1.1, U2.2 (SW)
unnamed: C16.1, R24.2, U3.1 (EN)
unnamed: R25.2, R26.2, U3.3 (FB)
unnamed: C17.1, U3.4 (SS)

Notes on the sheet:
USB conn
+25v
R_sense
BMS 3 cells
DC-DC +12V
+16v
ON/OFF SWITCH
NTC 10k
DC-DC +3.3V
Cells connector

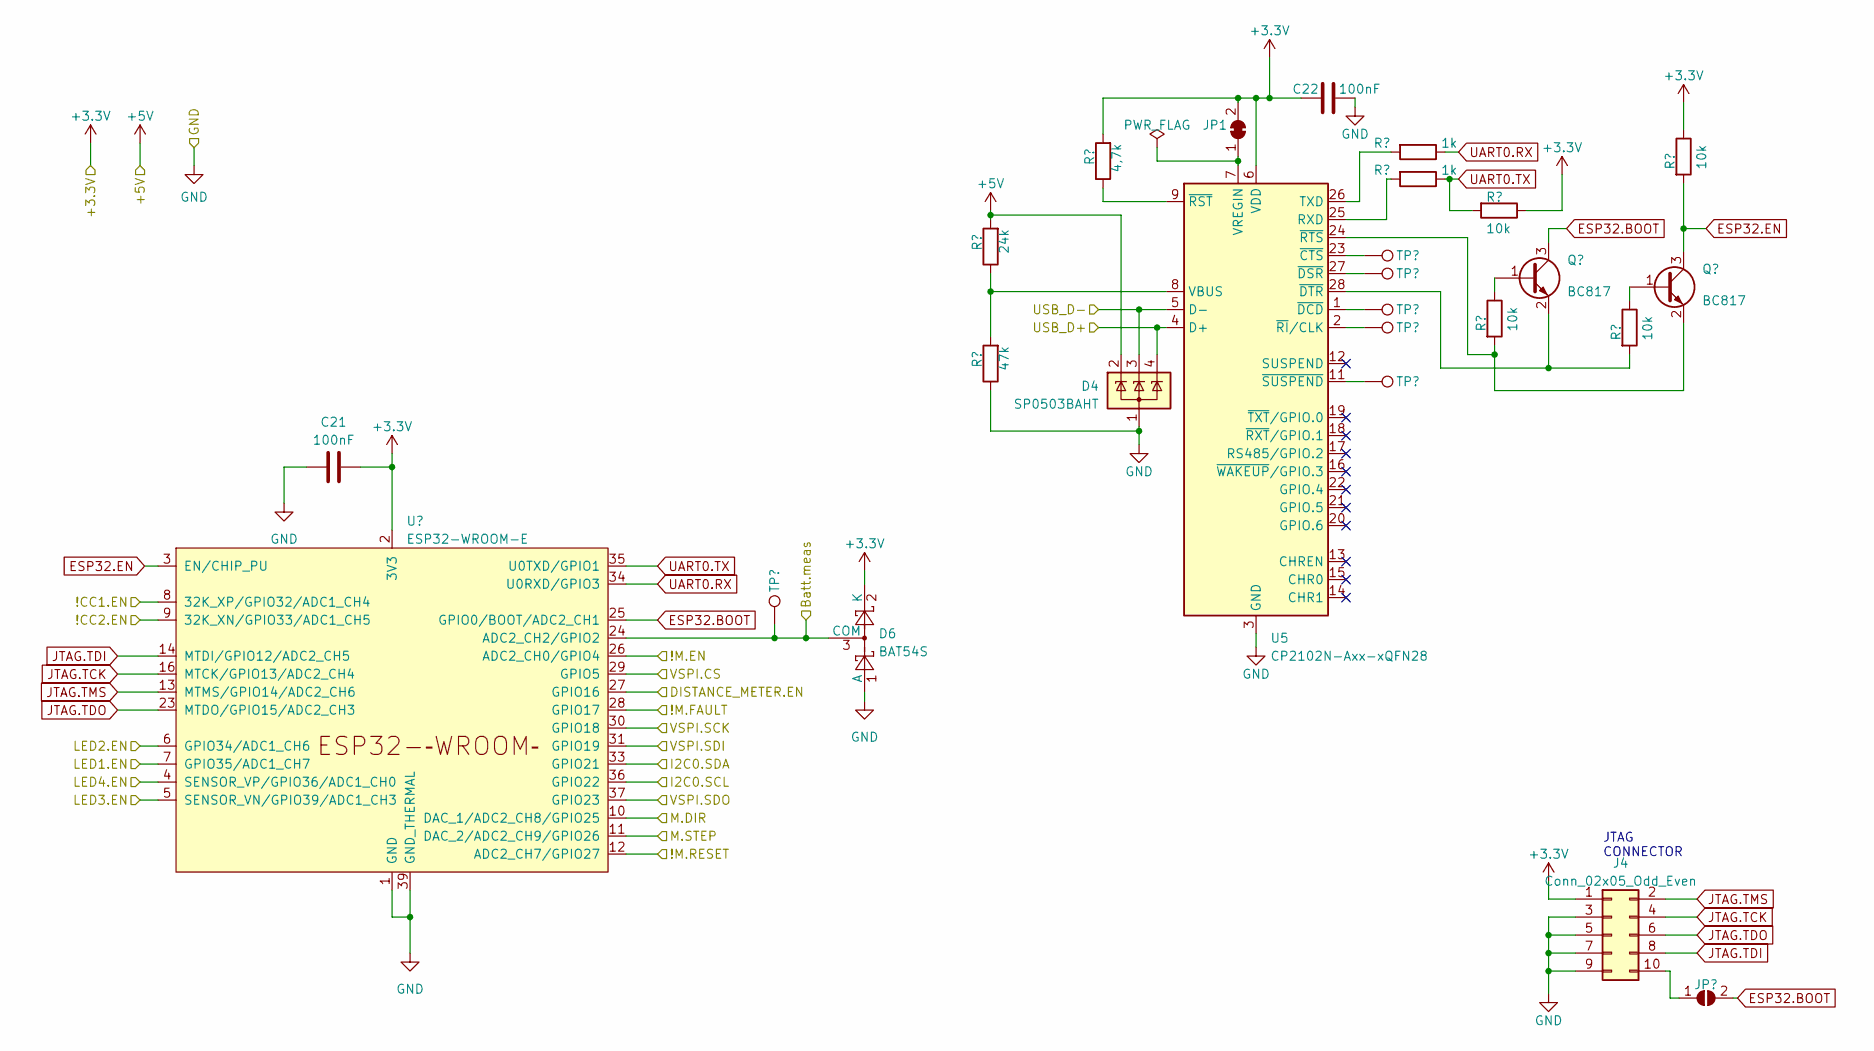
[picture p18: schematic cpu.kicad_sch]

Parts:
Batt.meas1: TestPoint; TestPoint_THTPad_1.0x1.0mm_Drill0.5mm
C21, C22: 100nF; C_0805_2012Metric_Pad1.18x1.45mm_HandSolder
D4: SP0503BAHT; SOT-143
D6: BAT54S; SOT-23
J4: Conn_02x05_Odd_Even; PinHeader_2x05_P2.00mm_Vertical
JP1: SolderJumper_2_Bridged; SolderJumper-2_P1.3mm_Bridged_RoundedPad1.0x1.5mm
JP2: SolderJumper_2_Open; SolderJumper-2_P1.3mm_Open_RoundedPad1.0x1.5mm
Q6, Q7: BC817; SOT-23
R27: 24k; R_0805_2012Metric_Pad1.20x1.40mm_HandSolder
R28: 47k; R_0805_2012Metric_Pad1.20x1.40mm_HandSolder
R29: 4,7k; R_0805_2012Metric_Pad1.20x1.40mm_HandSolder
R30, R31: 1k; R_0805_2012Metric_Pad1.20x1.40mm_HandSolder
R32, R33, R34, R50: 10k; R_0805_2012Metric_Pad1.20x1.40mm_HandSolder
TP3, TP4, TP5, TP6, TP7: TestPoint; TestPoint_THTPad_1.0x1.0mm_Drill0.5mm
U4: ESP32-WROOM-E; ESP32-WROOM-32E
U5: CP2102N-Axx-xQFN28; QFN-28-1EP_5x5mm_P0.5mm_EP3.35x3.35mm

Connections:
+3.3V: C21.2, C22.1, D6.2 (K), J4.1, JP1.2 (B), R29.2, R33.1, R50.1, U4.2 (3V3), U5.6 (VDD); also elsewhere on the board
+5V: D4.2 (K), R27.2; also elsewhere on the board
/CPU/!CC1.EN: U4.8 (32K_XP/GPIO32/ADC1_CH4); also elsewhere on the board
/CPU/!CC2.EN: U4.9 (32K_XN/GPIO33/ADC1_CH5); also elsewhere on the board
/CPU/!M.EN: U4.26 (ADC2_CH0/GPIO4); also elsewhere on the board
/CPU/!M.FAULT: U4.28 (GPIO17); also elsewhere on the board
/CPU/!M.RESET: U4.12 (ADC2_CH7/GPIO27); also elsewhere on the board
/CPU/DISTANCE_METER.EN: U4.27 (GPIO16); also elsewhere on the board
/CPU/I2C0.SCL: U4.36 (GPIO22); also elsewhere on the board
/CPU/I2C0.SDA: U4.33 (GPIO21); also elsewhere on the board
/CPU/LED1.EN: U4.7 (GPIO35/ADC1_CH7); also elsewhere on the board
/CPU/LED2.EN: U4.6 (GPIO34/ADC1_CH6); also elsewhere on the board
/CPU/LED3.EN: U4.5 (SENSOR_VN/GPIO39/ADC1_CH3); also elsewhere on the board
/CPU/LED4.EN: U4.4 (SENSOR_VP/GPIO36/ADC1_CH0); also elsewhere on the board
/CPU/M.DIR: U4.10 (DAC_1/ADC2_CH8/GPIO25); also elsewhere on the board
/CPU/M.STEP: U4.11 (DAC_2/ADC2_CH9/GPIO26); also elsewhere on the board
/CPU/USB_D+: D4.4 (K), U5.4 (D+); also elsewhere on the board
/CPU/USB_D-: D4.3 (K), U5.5 (D-); also elsewhere on the board
/CPU/VSPI.CS: U4.29 (GPIO5); also elsewhere on the board
/CPU/VSPI.SCK: U4.30 (GPIO18); also elsewhere on the board
/CPU/VSPI.SDI: U4.31 (GPIO19); also elsewhere on the board
/CPU/VSPI.SDO: U4.37 (GPIO23); also elsewhere on the board
ESP32.BOOT: JP2.2 (B), Q6.3 (C), U4.25 (GPIO0/BOOT/ADC2_CH1)
ESP32.EN: Q7.3 (C), R50.2, U4.3 (EN/CHIP_PU)
GND: C21.1, C22.2, D4.1 (A), D6.1 (A), J4.3, J4.5, J4.7, J4.9, R28.1, U4.1 (GND), U4.15 (GND), U4.38 (GND), U4.39 (GND_THERMAL), U5.3 (GND), U5.29 (GND); also elsewhere on the board
JTAG.TCK: J4.4, U4.16 (MTCK/GPIO13/ADC2_CH4)
JTAG.TDI: J4.8, U4.14 (MTDI/GPIO12/ADC2_CH5)
JTAG.TDO: J4.6, U4.23 (MTDO/GPIO15/ADC2_CH3)
JTAG.TMS: J4.2, U4.13 (MTMS/GPIO14/ADC2_CH6)
unnamed: J4.10, JP2.1 (A)
unnamed: JP1.1 (A), U5.7 (VREGIN)
unnamed: Q6.1 (B), R32.1
unnamed: Q7.1 (B), R34.1
unnamed: R31.2, U5.25 (RXD)
unnamed: R30.2, U5.26 (TXD)
unnamed: R27.1, R28.2, U5.8 (VBUS)
unnamed: TP3.1, U5.23 (~CTS)
unnamed: TP5.1, U5.1 (~DCD)
unnamed: TP4.1, U5.27 (~DSR)
unnamed: TP6.1, U5.2 (~RI/CLK)
unnamed: R29.1, U5.9 (~RST)
unnamed: TP7.1, U5.11 (~SUSPEND)
UART0.RX: R30.1, U4.34 (U0RXD/GPIO3)
UART0.TX: R31.1, R33.2, U4.35 (U0TXD/GPIO1)

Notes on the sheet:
JTAG CONNECTOR

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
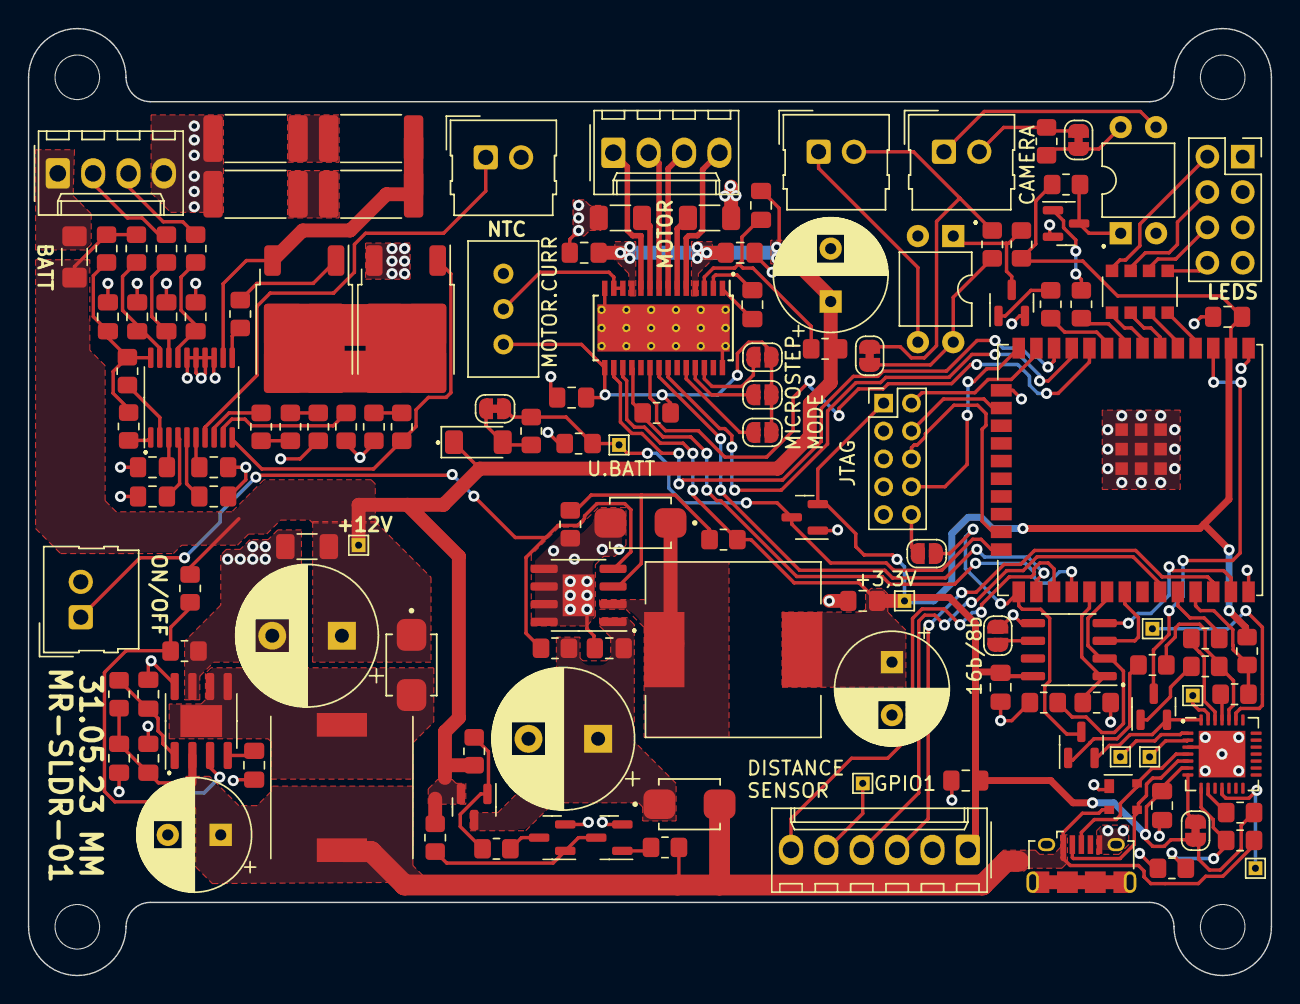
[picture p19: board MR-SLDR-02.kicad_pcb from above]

Board: 2 copper layers, 89.3 x 68.0 mm, 139 parts (0 on the bottom side), 118 nets.

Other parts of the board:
JP9: SolderJumper_2_Bridged; SolderJumper-2_P1.3mm_Bridged_RoundedPad1.0x1.5mm

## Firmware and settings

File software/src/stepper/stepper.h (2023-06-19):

/*
Copyright (c) 2023 Mikolaj Markiel

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
THE SOFTWARE IS PROVIDED "AS IS", WITHOUT WARRANTY OF ANY KIND, EXPRESS OR
IMPLIED, INCLUDING BUT NOT LIMITED TO THE WARRANTIES OF MERCHANTABILITY,
FITNESS FOR A PARTICULAR PURPOSE AND NONINFRINGEMENT. IN NO EVENT SHALL THE
AUTHORS OR COPYRIGHT HOLDERS BE LIABLE FOR ANY CLAIM, DAMAGES OR OTHER
LIABILITY, WHETHER IN AN ACTION OF CONTRACT, TORT OR OTHERWISE, ARISING FROM,
OUT OF OR IN CONNECTION WITH THE SOFTWARE OR THE USE OR OTHER DEALINGS IN THE
SOFTWARE.
*/

#ifndef __STEPPER_HEADER__
#define __STEPPER_HEADER__

#ifdef __cplusplus
extern "C" {
#endif

#include <stdio.h>
#include <zephyr/device.h>
#include <zephyr/drivers/counter.h>
#include <zephyr/drivers/gpio.h>
#include <zephyr/kernel.h>
#include <zephyr/logging/log.h>

#define SLIDER_STATUS_IDLE "Idle"
#define SLIDER_STATUS_RUNNING "Runn"
#define SLIDER_STATUS_HALTED "Halt"
#define SLIDER_STATUS_ERROR "Erro"
#define SLIDER_STATUS_CALIB "Cali"

#define STEPS_FACTOR 100 // <x> steps for 1 mm move
#define MIN_MOTOR_DELAY 50

#define DEFAULT_START_POS 0
#define DEFAULT_END_POS 50
#define DEFAULT_SPEED 1000
#define DEFAULT_DIR 1
#define DEFAULT_INTERVAL_STEPS 2
#define DEFAULT_INTERVAL_DELAY 250
#define DEFAULT_SOFT_START 500

typedef struct slider_params {
  char status[10];
  uint32_t dir;
  uint32_t start_pos;
  uint32_t end_pos;
  uint32_t duration;
  uint32_t speed;
  uint32_t steps;
  uint32_t interval_steps;
  uint32_t interval_delay;
  uint32_t soft_start;
} slider_params;

extern slider_params slider;

int stepper_motor_init(void);

void slider_stop();
int slider_calib();
void slider_thread();

#ifdef __cplusplus
}
#endif

#endif // __STEPPER_HEADER__

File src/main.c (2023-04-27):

/*
Copyright (c) 2023 Mikolaj Markiel

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
THE SOFTWARE IS PROVIDED "AS IS", WITHOUT WARRANTY OF ANY KIND, EXPRESS OR
IMPLIED, INCLUDING BUT NOT LIMITED TO THE WARRANTIES OF MERCHANTABILITY,
FITNESS FOR A PARTICULAR PURPOSE AND NONINFRINGEMENT. IN NO EVENT SHALL THE
AUTHORS OR COPYRIGHT HOLDERS BE LIABLE FOR ANY CLAIM, DAMAGES OR OTHER
LIABILITY, WHETHER IN AN ACTION OF CONTRACT, TORT OR OTHERWISE, ARISING FROM,
OUT OF OR IN CONNECTION WITH THE SOFTWARE OR THE USE OR OTHER DEALINGS IN THE
SOFTWARE.
*/

#include "stepper.h"
#include <zephyr/bluetooth/bluetooth.h>
#include <zephyr/bluetooth/conn.h>
#include <zephyr/bluetooth/gatt.h>
#include <zephyr/bluetooth/hci.h>
#include <zephyr/bluetooth/uuid.h>
#include <zephyr/device.h>
#include <zephyr/drivers/gpio.h>
#include <zephyr/kernel.h>
#include <zephyr/logging/log.h>

#include <stdint.h>
#include <stdio.h>
#include <stdlib.h>
#include <string.h>

LOG_MODULE_REGISTER(app);
static const struct gpio_dt_spec led =
    GPIO_DT_SPEC_GET(DT_NODELABEL(blinking_led), gpios);

#define SLIDER_UUID(num)                                                       \
  BT_UUID_128_ENCODE(0x12340000 | num, 0x1234, 0x5678, 0x1234,                 \
                     0x56789abcdef0) // TODO change to something more random

#define BT_UUID_SLIDER_SERVICE SLIDER_UUID(0x0000)

static struct bt_uuid_128 slider_service_uuid =
    BT_UUID_INIT_128(SLIDER_UUID(0x0000));
static struct bt_uuid_128 slider_status_uuid =
    BT_UUID_INIT_128(SLIDER_UUID(0x0001));
static struct bt_uuid_128 slider_cmd_uuid =
    BT_UUID_INIT_128(SLIDER_UUID(0x0002));
static struct bt_uuid_128 slider_start_pos_uuid =
    BT_UUID_INIT_128(SLIDER_UUID(0x0010));
static struct bt_uuid_128 slider_end_pos_uuid =
    BT_UUID_INIT_128(SLIDER_UUID(0x0011));
static struct bt_uuid_128 slider_duration_uuid =
    BT_UUID_INIT_128(SLIDER_UUID(0x0012));
static struct bt_uuid_128 slider_speed_uuid =
    BT_UUID_INIT_128(SLIDER_UUID(0x0013));

static const struct bt_data ad[] = {
    BT_DATA_BYTES(BT_DATA_FLAGS, (BT_LE_AD_GENERAL | BT_LE_AD_NO_BREDR)),
    BT_DATA_BYTES(BT_DATA_UUID128_ALL, BT_UUID_SLIDER_SERVICE),
    BT_DATA_BYTES(BT_DATA_NAME_COMPLETE, CONFIG_BT_DEVICE_NAME),
};

static const struct bt_data sd[] = {
    BT_DATA_BYTES(BT_DATA_FLAGS, (BT_LE_AD_GENERAL | BT_LE_AD_NO_BREDR)),
    BT_DATA_BYTES(BT_DATA_UUID128_ALL, BT_UUID_SLIDER_SERVICE),
    BT_DATA_BYTES(BT_DATA_NAME_COMPLETE, CONFIG_BT_DEVICE_NAME),
};

#define DEFAULT_WR_PROPS                                                       \
  BT_GATT_CHRC_READ | BT_GATT_CHRC_WRITE | BT_GATT_CHRC_NOTIFY |               \
      BT_GATT_CHRC_AUTH
#define DEFAULT_WR_PERMS BT_GATT_PERM_READ | BT_GATT_PERM_WRITE

#define DEFAULT_RO_PROPS                                                       \
  BT_GATT_CHRC_READ | BT_GATT_CHRC_NOTIFY | BT_GATT_CHRC_AUTH
#define DEFAULT_RO_PERMS BT_GATT_PERM_READ

#define DEFAULT_WO_PROPS BT_GATT_CHRC_WRITE | BT_GATT_CHRC_AUTH
#define DEFAULT_WO_PERMS BT_GATT_PERM_WRITE

static ssize_t write_int_param(struct bt_conn *conn,
                               const struct bt_gatt_attr *attr, const void *buf,
                               uint16_t len, uint16_t offset, uint8_t flags) {
  uint32_t *param = attr->user_data;
  static uint32_t temp;
  char value_1[10]; // TODO - change magical 10 to max BCD signs of uint32_t
                    // (4294967296);
  char value_2[10];
  memcpy(value_1, buf, len);
  value_1[len] = 0;
  temp = atoi(value_1);
  sprintf(value_2, "%d", temp);
  if (strcmp(value_1, value_2)) {
    LOG_ERR("wrong int value, val_1: %s, val_2: %s", value_1, value_2);
    return BT_GATT_ERR(BT_ATT_ERR_VALUE_NOT_ALLOWED);
  }
  memcpy(param, &temp, sizeof(*param));
  LOG_INF("write value, int: %d", *param);
  return len;
}

static ssize_t read_int_param(struct bt_conn *conn,
                              const struct bt_gatt_attr *attr, void *buf,
                              uint16_t len, uint16_t offset) {
  uint32_t *param = attr->user_data;
  char value[sizeof(uint32_t)];
  sprintf(value, "%d", *param);
  LOG_INF("read value, int: %d, str: %s", *param, value);
  return bt_gatt_attr_read(conn, attr, buf, len, offset, value, strlen(value));
}

static ssize_t cmd_handler(struct bt_conn *conn,
                           const struct bt_gatt_attr *attr, const void *buf,
                           uint16_t len, uint16_t offset, uint8_t flags) {
  uint32_t cmd;
  if (len > sizeof(cmd)) {
    LOG_ERR("wrong cmd input!");
    memcpy(slider_status.status, SLIDER_STATUS_ERROR, 4);
    return len;
  }
  memcpy(&cmd, buf, len);

  LOG_INF("cmd handler cmd %d, len: %d", cmd, len);
  switch (cmd) {
  case '1': {
    memcpy(slider_status.status, SLIDER_STATUS_RUNNING, 4);
    break;
  }
  case '2': {
    memcpy(slider_status.status, SLIDER_STATUS_HALTED, 4);
    break;
  }
  default: {
    break;
  }
  }
  return len;
}

static void ct_ccc_changed(const struct bt_gatt_attr *attr, uint16_t value) {
  /* TODO: Handle value */
}

BT_GATT_SERVICE_DEFINE(
    slider_service, BT_GATT_PRIMARY_SERVICE(&slider_service_uuid.uuid),
    BT_GATT_CHARACTERISTIC(&slider_status_uuid.uuid, DEFAULT_RO_PROPS,
                           DEFAULT_RO_PERMS, read_int_param, write_int_param,
                           &slider_status.status),
    BT_GATT_CCC(ct_ccc_changed, BT_GATT_PERM_READ | BT_GATT_PERM_WRITE),
    BT_GATT_CHARACTERISTIC(&slider_start_pos_uuid.uuid, DEFAULT_WR_PROPS,
                           DEFAULT_WR_PERMS, read_int_param, write_int_param,
                           &slider_status.start_pos),
    BT_GATT_CCC(ct_ccc_changed, BT_GATT_PERM_READ | BT_GATT_PERM_WRITE),
    BT_GATT_CHARACTERISTIC(&slider_end_pos_uuid.uuid, DEFAULT_WR_PROPS,
                           DEFAULT_WR_PERMS, read_int_param, write_int_param,
                           &slider_status.end_pos),
    BT_GATT_CCC(ct_ccc_changed, BT_GATT_PERM_READ | BT_GATT_PERM_WRITE),
    BT_GATT_CHARACTERISTIC(&slider_duration_uuid.uuid, DEFAULT_WR_PROPS,
                           DEFAULT_WR_PERMS, read_int_param, write_int_param,
                           &slider_status.duration),
    BT_GATT_CCC(ct_ccc_changed, BT_GATT_PERM_READ | BT_GATT_PERM_WRITE),
    BT_GATT_CHARACTERISTIC(&slider_speed_uuid.uuid, DEFAULT_WR_PROPS,
                           DEFAULT_WR_PERMS, read_int_param, write_int_param,
                           &slider_status.speed),
    BT_GATT_CCC(ct_ccc_changed, BT_GATT_PERM_READ | BT_GATT_PERM_WRITE),

    BT_GATT_CHARACTERISTIC(&slider_cmd_uuid.uuid, DEFAULT_WO_PROPS,
                           DEFAULT_WO_PERMS, NULL, cmd_handler, NULL), );

#define NOTIFY_SLIDER_STATUS 2
#define NOTIFY_SLIDER_START_POS NOTIFY_SLIDER_STATUS + 3
#define NOTIFY_SLIDER_END_POS NOTIFY_SLIDER_START_POS + 3
#define NOTIFY_SLIDER_DURATION NOTIFY_SLIDER_END_POS + 3
#define NOTIFY_SLIDER_SPEED NOTIFY_SLIDER_DURATION + 3

uint8_t bt_conn_cnt = 0;
void bt_notify_differences(const struct bt_gatt_attr *chrc,
                           const void *current_msg, void *old_msg, size_t n) {
  static int err;
  static uint8_t old_bt_conn_cnt = 0;
  if (!bt_conn_cnt) {
    return;
  }
  if (!memcmp(old_msg, current_msg, n)) {
    return;
  }
  memcpy(old_msg, current_msg, n);
  err = bt_gatt_notify(NULL, chrc, old_msg, sizeof(old_msg));
  err =
      err == -ENOTCONN ? 0 : err; // TODO exchange if server has opportunity to
                                  // know that client notification is enabled
  if (err) {
    LOG_ERR("gatt notify failed, reason: %d", err);
    return;
  }
  LOG_INF("gatt notify successful");
}

void bt_notify_handler() { // TODO: write to a thread
  while (1) {
    static slider_params old_slider_status;
    bt_notify_differences(&slider_service.attrs[NOTIFY_SLIDER_STATUS],
                          &slider_status.status, &old_slider_status.status,
                          sizeof(slider_status.status));
    bt_notify_differences(&slider_service.attrs[NOTIFY_SLIDER_START_POS],
                          &slider_status.start_pos,
                          &old_slider_status.start_pos,
                          sizeof(slider_status.start_pos));
    bt_notify_differences(&slider_service.attrs[NOTIFY_SLIDER_END_POS],
                          &slider_status.end_pos, &old_slider_status.end_pos,
                          sizeof(slider_status.end_pos));
    bt_notify_differences(&slider_service.attrs[NOTIFY_SLIDER_DURATION],
                          &slider_status.duration, &old_slider_status.duration,
                          sizeof(slider_status.duration));
    bt_notify_differences(&slider_service.attrs[NOTIFY_SLIDER_SPEED],
                          &slider_status.speed, &old_slider_status.speed,
                          sizeof(slider_status.speed));
    k_msleep(100);
  }
}

K_THREAD_DEFINE(bt_notifications, 1024, bt_notify_handler, NULL, NULL, NULL, 7,
                0, 0);

static void connected(struct bt_conn *conn, uint8_t err) {
  if (err) {
    printk("Connection failed (err %u)\n", err);
    return;
  }
  bt_conn_cnt++;
  LOG_INF("Connected, current connections: %d", bt_conn_cnt);
}

static void disconnected(struct bt_conn *conn, uint8_t reason) {
  if (bt_conn_cnt > 0) {
    bt_conn_cnt--;
  }
  LOG_INF("Disconnected (reason %u), current connections: %d", reason,
          bt_conn_cnt);
}

BT_CONN_CB_DEFINE(conn_callbacks) = {
    .connected = connected,
    .disconnected = disconnected,
};

static void auth_passkey_display(struct bt_conn *conn, unsigned int passkey) {
  char addr[BT_ADDR_LE_STR_LEN];

  bt_addr_le_to_str(bt_conn_get_dst(conn), addr, sizeof(addr));

  printk("Passkey for %s: %06u\n", addr, passkey);
}

static void auth_cancel(struct bt_conn *conn) {
  char addr[BT_ADDR_LE_STR_LEN];

  bt_addr_le_to_str(bt_conn_get_dst(conn), addr, sizeof(addr));

  printk("Pairing cancelled: %s\n", addr);
}

static struct bt_conn_auth_cb auth_cb_display = {
    .passkey_display = auth_passkey_display,
    .passkey_entry = NULL,
    .cancel = auth_cancel,
};

K_THREAD_DEFINE(slider_process_id, 1024, slider_process_thread, NULL, NULL,
                NULL, 3, 0, 0);

int led_test_init() {
  int err;
  if (!gpio_is_ready_dt(&led)) {
    LOG_ERR("led gpio isn't ready");
    return 1;
  }
  err = gpio_pin_configure_dt(&led, GPIO_OUTPUT_ACTIVE);
  if (err < 0) {
    LOG_ERR("gpio_pin_configure_dt failed");
    return 2;
  }
  return 0;
}

void main(void) {
  int err;
  err = stepper_motor_gpio_init();
  if (err) {
    return;
  }
  err = led_test_init();
  if (err) {
    return;
  }

  err = bt_enable(NULL);
  if (err) {
    LOG_ERR("Bluetooth init failed (err %d)", err);
    return;
  }

  err = bt_conn_auth_cb_register(&auth_cb_display);
  if (err) {
    LOG_ERR("bt_conn_auth_cb_register failed: (err %d)", err);
    return;
  }

  err = bt_le_adv_start(BT_LE_ADV_CONN, ad, ARRAY_SIZE(ad), sd, ARRAY_SIZE(sd));
  if (err) {
    LOG_ERR("Advertising failed to start (err %d)", err);
    return;
  }

  LOG_INF("Advertising started succesfully");

  while (1) {
    gpio_pin_toggle_dt(&led);
    k_msleep(1000);
    if (!memcmp(slider_status.status, SLIDER_STATUS_HALTED, 4)) {
      memcpy(slider_status.status, SLIDER_STATUS_IDLE, 4);
    }
  }
}

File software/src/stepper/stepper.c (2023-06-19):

/*
Copyright (c) 2023 Mikolaj Markiel

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
THE SOFTWARE IS PROVIDED "AS IS", WITHOUT WARRANTY OF ANY KIND, EXPRESS OR
IMPLIED, INCLUDING BUT NOT LIMITED TO THE WARRANTIES OF MERCHANTABILITY,
FITNESS FOR A PARTICULAR PURPOSE AND NONINFRINGEMENT. IN NO EVENT SHALL THE
AUTHORS OR COPYRIGHT HOLDERS BE LIABLE FOR ANY CLAIM, DAMAGES OR OTHER
LIABILITY, WHETHER IN AN ACTION OF CONTRACT, TORT OR OTHERWISE, ARISING FROM,
OUT OF OR IN CONNECTION WITH THE SOFTWARE OR THE USE OR OTHER DEALINGS IN THE
SOFTWARE.
*/

#include "stepper.h"
#include "rangefinder.h"
#include <string.h>
#include <zephyr/device.h>
#include <zephyr/drivers/counter.h>
#include <zephyr/drivers/gpio.h>
#include <zephyr/kernel.h>
#include <zephyr/logging/log.h>

#define TIMER timer0
#define ALARM_CHANNEL_ID 0

#define STEPPER_MOTOR_ENABLE() gpio_pin_set_dt(&stepper_motor_en, 0)
#define STEPPER_MOTOR_DISABLE() gpio_pin_set_dt(&stepper_motor_en, 1)

#define CB_FOR_ONE_STEP 2
#define US_IN_ONE_SEC 1000000
#define CB_DELAY(speed) US_IN_ONE_SEC / speed / CB_FOR_ONE_STEP

#define CALIB_MAX_STEPS 0xFFFFFFFF
#define CALIB_SLIDER_SPEED 500
#define CALIB_STEPS_DELAY CB_DELAY(CALIB_SLIDER_SPEED)

LOG_MODULE_REGISTER(stepper);

typedef struct {
  uint32_t c_step;
  uint32_t c_delay;
  uint32_t c_interval;
  uint32_t max_delay;
  uint32_t min_delay;
} stepper_thread_data;

typedef enum {
  FORWARD = 0,
  REVERSE = 1,
} T_DIR;

const struct device *const counter_dev = DEVICE_DT_GET(DT_NODELABEL(TIMER));

slider_params slider;

static struct counter_alarm_cfg alarm_cfg;
static uint32_t timer_status;
static uint32_t steps;

static const struct gpio_dt_spec stepper_motor_step =
    GPIO_DT_SPEC_GET(DT_NODELABEL(stepper_motor_step), gpios);
static const struct gpio_dt_spec stepper_motor_dir =
    GPIO_DT_SPEC_GET(DT_NODELABEL(stepper_motor_dir), gpios);
static const struct gpio_dt_spec stepper_motor_en =
    GPIO_DT_SPEC_GET(DT_NODELABEL(stepper_motor_en), gpios);

static int timer_enable(const struct device *dev) {
  int err;
  err = counter_start(dev);
  if (err == 0) {
    timer_status = 1;
  }
  return err;
}

static int timer_disable(const struct device *dev) {
  int err;
  err = counter_stop(dev);
  if (err == 0) {
    timer_status = 0;
  }
  return err;
}

static void select_dir(slider_params *slider) {
  if (slider->end_pos > slider->start_pos) {
    slider->dir = FORWARD;
  } else {
    slider->dir = REVERSE;
  }
}

static void count_steps(slider_params *slider) {
  select_dir(slider);
  if (slider->dir == FORWARD) {
    slider->steps = (slider->end_pos - slider->start_pos) * STEPS_FACTOR;
  } else {
    slider->steps = (slider->start_pos - slider->end_pos) * STEPS_FACTOR;
  }
}

static void count_duration(slider_params *slider) {
  // TODO
  slider->duration = 0;
}

static void slider_init_params(slider_params *slider) {
    memcpy(slider->status, SLIDER_STATUS_IDLE, sizeof(SLIDER_STATUS_IDLE));
  // memcpy(slider->status, SLIDER_STATUS_CALIB, sizeof(SLIDER_STATUS_CALIB));
  slider->start_pos = DEFAULT_START_POS;
  slider->end_pos = DEFAULT_END_POS;
  slider->speed = DEFAULT_SPEED;
  slider->dir = DEFAULT_DIR;
  slider->interval_steps = DEFAULT_INTERVAL_STEPS;
  slider->interval_delay = DEFAULT_INTERVAL_DELAY;
  slider->soft_start = DEFAULT_SOFT_START;
  count_steps(slider);
  count_duration(slider);
}

static int stepper_gpio_configure(const struct gpio_dt_spec *pin, char *name) {
  int err;
  if (!gpio_is_ready_dt(pin)) {
    LOG_ERR("%s gpio isn't ready", name);
    return 1;
  }
  err = gpio_pin_configure_dt(pin, GPIO_OUTPUT_ACTIVE);
  if (err < 0) {
    LOG_ERR("%s gpio configure failed", name);
    return err;
  }
  return 0;
}

static void counter_callback(const struct device *counter_dev, uint8_t chan_id,
                             uint32_t ticks, void *user_data) {
  static uint8_t pin_state = 0;
  stepper_thread_data *data = user_data;

  pin_state ^= 1;
  data->c_step -= (pin_state == 0) ? 1 : 0;
  gpio_pin_set_dt(&stepper_motor_step, pin_state);
  if (data->c_step == 0) {
    timer_disable(counter_dev);
    STEPPER_MOTOR_DISABLE();
    return;
  }

  if (data->max_delay - data->c_delay >= data->c_step) {
    data->c_delay++;
  } else if (data->c_delay > data->min_delay) {
    data->c_delay--;
  }

  alarm_cfg.ticks = counter_us_to_ticks(counter_dev, data->c_delay);
  counter_set_channel_alarm(counter_dev, ALARM_CHANNEL_ID, &alarm_cfg);
  return;
}

static int set_interval_process(stepper_thread_data *data) {
  int err;
  uint32_t delay_speed;
  uint32_t delay_soft;
  const uint32_t min_delay = counter_us_to_ticks(counter_dev, MIN_MOTOR_DELAY);

  //   if (memcmp(slider.status, SLIDER_STATUS_RUNNING, 4)) {
  //     return -1;
  //   }
  if (slider.speed == 0) {
    LOG_ERR("invalid speed value");
    return -2;
  }
  delay_speed = CB_DELAY(slider.speed);
  data->c_delay = delay_speed > min_delay ? delay_speed : min_delay;
  data->min_delay = data->c_delay;

  if (slider.soft_start != 0) {
    delay_soft = CB_DELAY(slider.soft_start);
  } else {
    delay_soft = 0;
  }
  data->c_delay = delay_speed > delay_soft ? delay_speed : delay_soft;
  data->max_delay = data->c_delay;

  alarm_cfg.ticks = counter_us_to_ticks(counter_dev, delay_speed);

  gpio_pin_set_dt(&stepper_motor_dir, slider.dir);
  STEPPER_MOTOR_ENABLE();

  err = timer_enable(counter_dev);
  if (err) {
    LOG_ERR("timer_enable failed");
  }
  err = counter_set_channel_alarm(counter_dev, ALARM_CHANNEL_ID, &alarm_cfg);
  if (err) {
    LOG_ERR("counter set channel alarm failed");
  }
  return 0;
}

int stepper_motor_init(void) {
  int err;
  err = stepper_gpio_configure(&stepper_motor_step, "stepper_motor_step");
  if (err) {
    return err;
  }
  err = stepper_gpio_configure(&stepper_motor_dir, "stepper_motor_dir");
  if (err) {
    return err;
  }
  err = stepper_gpio_configure(&stepper_motor_en, "stepper_motor_en");
  if (err) {
    return err;
  }

  err = gpio_pin_set_dt(&stepper_motor_step, 0); // TODO set in dt
  if (err) {
    return err;
  }

  slider_init_params(&slider);
  if (!device_is_ready(counter_dev)) {
    LOG_ERR("counter_dev not ready.\n");
    return -ENODEV;
  }

  alarm_cfg.flags = 0;
  alarm_cfg.callback = counter_callback;

  return 0;
}

void slider_stop() {
  LOG_INF("process stopped");
  memcpy(slider.status, SLIDER_STATUS_HALTED, 4);
  timer_disable(counter_dev);
  STEPPER_MOTOR_DISABLE();
}
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

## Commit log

2023-05-08 v0.2 - switch to hardware timer peripheral, modified counter_esp32_tmr.c driver, reorganize repositorium
2023-05-13 v0.3 slider thread config correction
    [main.c, stepper.c, stepper.h]
2023-05-13 v0.5 added stepper motor soft start feature
2023-05-15 v0.6 added soft start & intervals to interface and some code corrections
    [main.c, stepper.c, stepper.h]
2023-05-16 added hardware concept
    [MR_SLDR.kicad_pcb, MR_SLDR.kicad_sch, cpu.kicad_sch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]
2023-06-02 finalized hardware design MR-SLDR-01
    [MR-SLDR-01-B_Cu.gbr, MR-SLDR-01-B_Mask.gbr, MR-SLDR-01-B_Paste.gbr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]
2023-06-07 v0.8 MM added rangefinder; move bt handler from main.c to slider_bt.c
    [MR-SLDR-01-B_Cu.gbr, MR-SLDR-01-B_Mask.gbr, MR-SLDR-01-B_Paste.gbr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]
2023-06-19 added prototype of calibration procedure
2023-06-19 fixed differences between BT notify and BT read procedures
    [main.c]
2023-06-20 fixed communication, maintained connection, check if device is disconnected
    [main.c]
